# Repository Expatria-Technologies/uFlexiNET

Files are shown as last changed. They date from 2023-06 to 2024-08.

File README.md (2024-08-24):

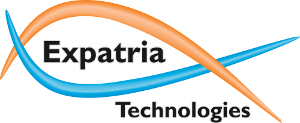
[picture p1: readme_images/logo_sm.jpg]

# uFlexiNET Ethernet and SD card module for FlexiHAL
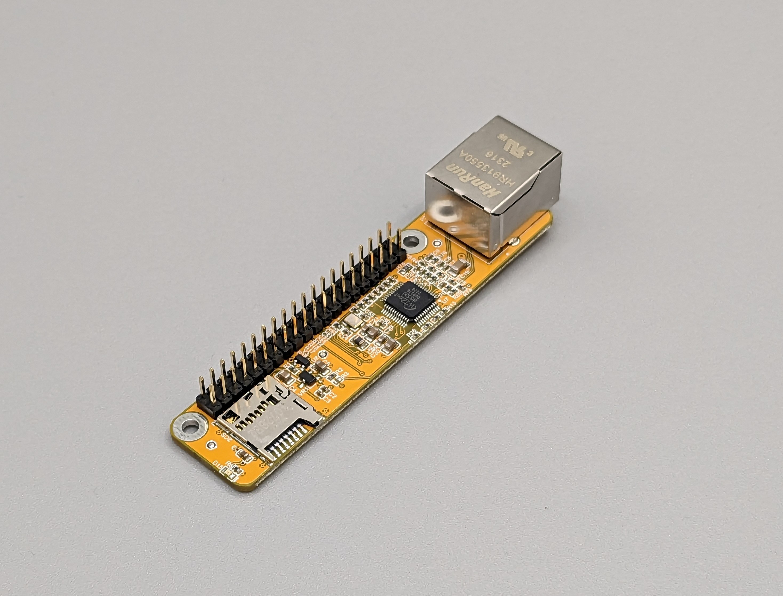
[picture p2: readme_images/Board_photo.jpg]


Adds Ethernet and SD card storage to a FlexiHAL CNC Controller

Currently available in our online store:

[https://expatria.myshopify.com/products/uflexinet](https://expatria.myshopify.com/products/uflexinet-ethernet-and-sd-card-module-for-flexihal)

Please consider buying a board to support our open-source designs. 

This module is designed to be installed on the 40 pin GPIO header of the FlexiHAL CNC controller.  It adds a uSD card interface and an Ethernet interface to the platform.  This brings compatbility with the SD card and Networking plugins with GRBLHAL.  Notably, this allows the use of named files for subroutines, probing routines and automatic toolchanging functions in GRBLHAL.  In addition, the module allows the user to connect compatible senders via Websockets (recomended) or Telnet.  The MQTT plugin can also be used if custom plugin code is written.

To use Remora with this module, users are responsible for researching and compiling their own components.

Optimized GRBLHAL driver is located here.  Look for releases with "ETH" in the name to use this module:  
https://github.com/Expatria-Technologies/STM32F4xx/releases

LinuxCNC/Remora port for uFlexiNET on the FlexiHAL controller is located here:  
https://github.com/Expatria-Technologies/Remora-STM32F4xx-W5500

### Installation
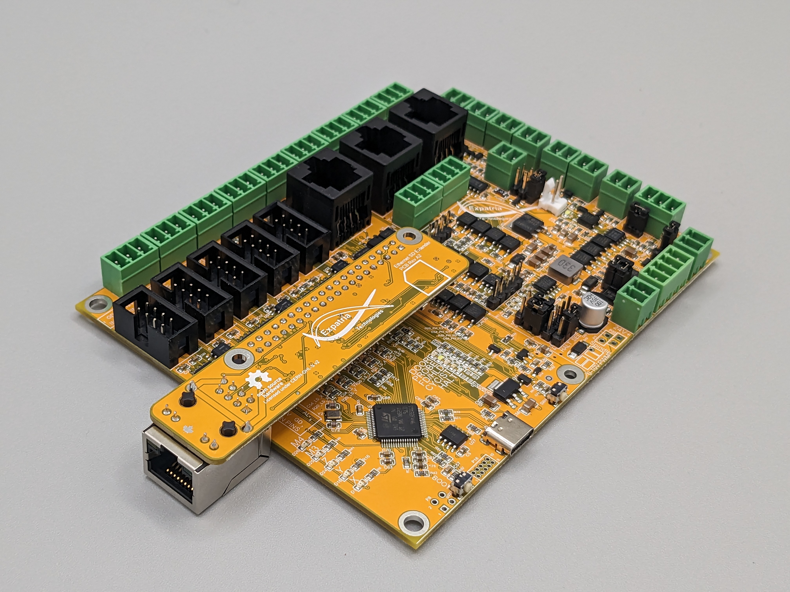
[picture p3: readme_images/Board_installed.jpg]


Disconnect power (main and USB) to the FlexiHAL and install the module in the GPIO header as shown above.  Be aware of excess cable strain (especially with heavy shielded CAT6 Ethernet cables and install spacers, fasteners and strain relief as needed.  If installing an SD card it is recommended to insert it before attaching the uFlexiNET to the mainboard as it is easier to ensure that it has the correct orientation.  Ensure the SD card is formatted as FAT32 and subsequent file operations (upload, delete) can be done via FTP over Ethernet or via the Ymodem protocol in senders like IOSender.

Note that the MCU on Flexi still needs 5V power supplied.  Normally this is via the USBC connector but it is also possible to jumper the 5V bypass pins on flexi to use the onboard 5V regulator.  Please note that this bypasses the galvanic isolation of FLexi and is not generally recommended.  See the FlexiHAL Readme for details:
https://github.com/Expatria-Technologies/Flexi-HAL#power-input

### Usage

Ensure that you flash appropriate GRBLHAL or Remora firmware to your FlexiHAL after installation.  See GRBLHAL and Remora documentation for further usage examples.

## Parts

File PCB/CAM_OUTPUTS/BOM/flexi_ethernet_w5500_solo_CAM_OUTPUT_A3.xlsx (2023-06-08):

Quantity | Manufacturer Part Number 1 | Manufacturer 1 | Description | SuppliersPartNumber | Package | Comment | Designator | Footprint
3 |  |  | Chip capacitors | C19666 | 0603 | 4.7uF | C1, C21, C48 | 0603_C
2 |  |  | Chip capacitor | C52923 | 0402 | 1.0uF | C2, C10 | 0402_C
8 |  |  | Chip capacitors | C1525 | 0402 | 100nF | C3, C22, C23, C24, C25, C26, C29, C50 | 0402_C
4 |  |  | Chip capacitors | C2922481 | 0805 | 22uF | C4, C5, C20, C30 | 0805_C
2 |  |  | Chip capacitors | C15195 | 0402 | 10nF | C6, C53 | 0402_C
2 |  |  | Chip capacitors | C1542 | 0402 | 6.8nF | C7, C8 | 0402_C
1 |  |  | Chip capacitors | C1532 | 0402 | 22nF | C9 | 0402_C
1 |  |  | Chip capacitors | C35216 | 1206 | 1nF | C19 | 1206_C
1 |  |  | Chip capacitor | C23733 | 0402 | 4.7uF | C51 | 0402_C
2 |  |  | Chip capacitors | C32949 | 0402 | 10pF | C54, C55 | 0402_C
1 |  |  | LED | C72043 | 0603 | 0603 Green | D15 | 0603_LED_S1
1 |  |  | 220Ω @ 100MHz 1 2A 150mΩ 0805 Ferrite Beads ROHS | C139188 | 0805 | 220Ω @ 100MHz 1 2A | L6 | 0805_C
1 |  |  | HR911105A Ethernet Interface Arduino Platform Evaluation Expansion Board | C163507 | None | Magjack | P2 | HANRUN_HR911105A
1 |  |  | Header, 20-Pin, Dual row | C124383 |  | Header 20X2 | P3 | HDR2X20_2.54_180
3 |  |  | Chip resistor | C17168 | 0402 | 0Ω ±1% | R1, R2, R18 | 0402_R
4 |  |  | Chip resistor | C25120 | 0402 | 49.9Ω ±1% | R4, R5, R74, R75 | 0402_R
1 |  |  | Chip resistor | C25900 | 0402 | 4.7KΩ ±1% | R6 | 0402_R
2 |  |  | Chip resistor | C25104 | 0402 | 330Ω ±1% | R12, R16 | 0402_R
4 |  |  | Chip resistor | C25744 | 0402 | 10KΩ ±1% | R13, R14, R15, R26 | 0402_R
1 |  |  | Chip resistor | C26083 | 0402 | 1MΩ ±1% | R17 | 0402_R
4 |  |  | Chip resistor | C25105 | 0402 | 33Ω ±1% | R69, R70, R73, R77 | 0402_R
1 |  |  | Chip resistor | C25077 | 0402 | 10Ω ±1% | R76 | 0402_R
1 |  |  | Chip resistor | C22865 | 0603 | 12.4KΩ ±1% | R78 | 0603_R
1 |  |  | Micro SD Connector, Pitch 1.1 mm, 8 Position, Height 1.4 mm, -25 to 85 degC, RoHS, Tape and Reel | C428492 |  | 503398-1892 | SD2 | MOLX-503398-1892_V
1 |  |  | Ethernet Controllers 2.97V ~ 3.63V 10/100 Base-T/TX PHY SPI LQFP-48_7x7x05P Ethernet ICs ROHS | C32843 | LQFP-48_7x7x05P | W5500 | U7 | LQFP-48_7x7x05P
1 |  |  | IC MPU SUPERVISORY 2.93V SOT23 | C9965 | 318-08 | MAX809STRG | U8 | FP-318-08-MFG
1 |  |  | 200mA 680mV@(100mA) Fixed 3.3V~3.3V Positive 1 6V SOT-23-3L Linear Voltage Regulators (LDO) ROHS | C5446 | SOT-23 | XC6206P332MR | VR1 | SOT-23-3L
1 |  |  | Crystal or Oscillator | C13740 |  | 25.0 MHz | Y3 | YSX321SL

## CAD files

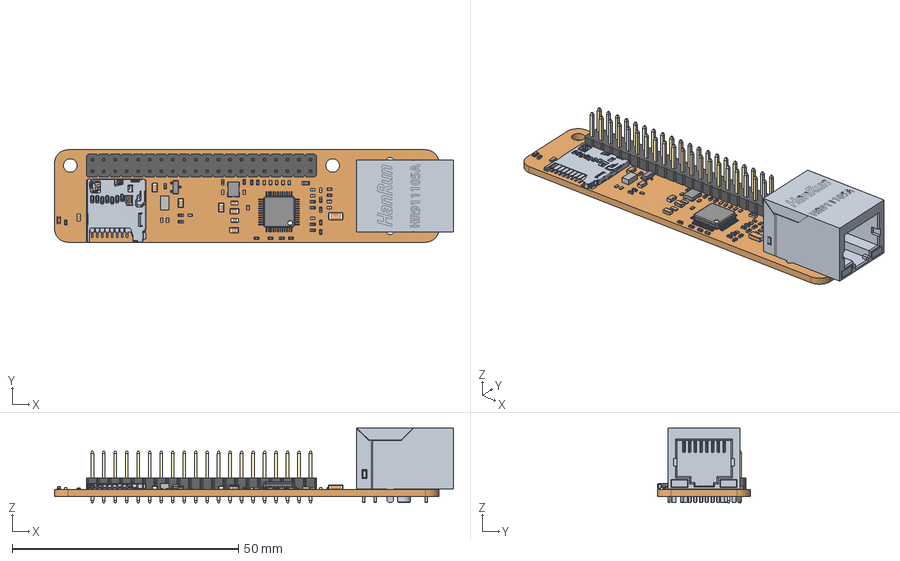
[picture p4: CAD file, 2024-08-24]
uFlexiNet.step
88.2 x 20.5 x 16.5 mm
0402 SMD Capacitor x 18
User Library-RES_1005-0402 x 21
Extruded
User Library-0805 SMD Capacitor x 5
User Library-0603 SMD Capacitor x 3
User Library-RES_1609-0603
User Library-LED_0603_R_Pocket002
User Library-LED_0603_R_Pad004
User Library-LED_0603_R_Fillet
User Library-LED_0603_R_Pocket001
User Library-LED_0603_R_Pad
C1206
pin_header_awl254-dg-g40d
Pins
QFP48P50_900X900X160L60X19N

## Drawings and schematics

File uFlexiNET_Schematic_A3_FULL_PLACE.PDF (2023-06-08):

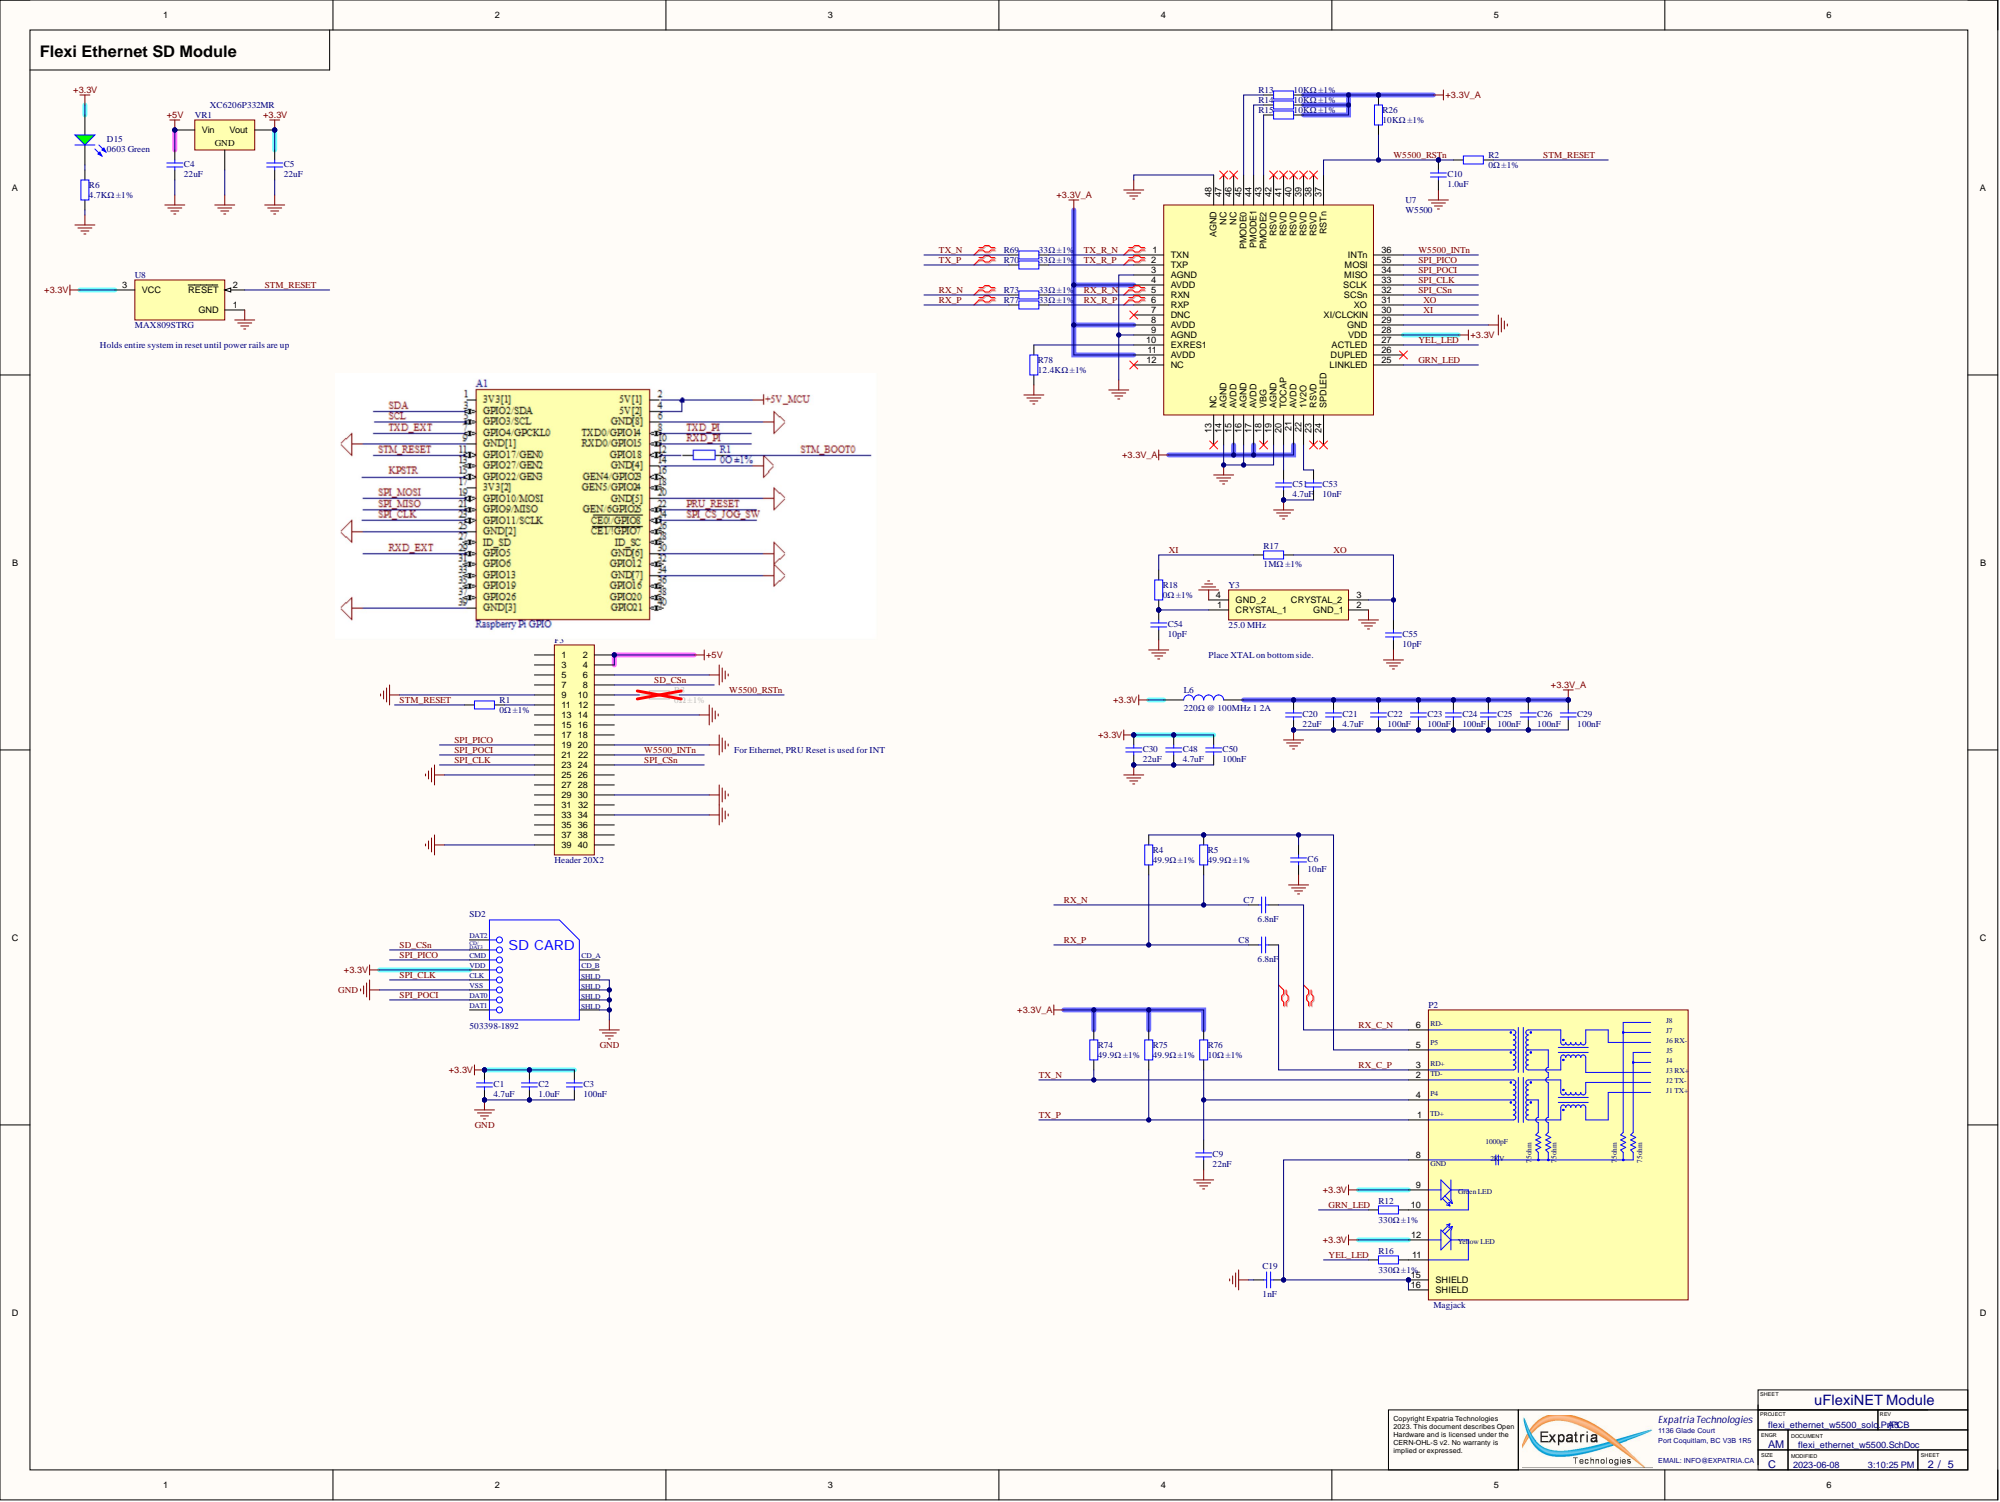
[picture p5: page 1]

Flexi Ethernet SD Module

R14 | 10KΩ ±1%
R15 | 10KΩ ±1%

RSTn 37 RSVD 38 RSVD 39 RSVD 40 RSVD 41 RSVD 42 PMODE2 43 PMODE1 44 PMODE0 45 NC 46 NC 47 AGND 48

SPDLED 24 LINKLED 25 DUPLED 26 ACTLED 27 VDD 28 GND 29 XI/CLCKIN 30 XO 31 SCSn 32 SCLK 33 MISO 34 MOSI 35 INTn 36

TX_R_P | TXP 2

AGND 3
AVDD 4

RX_R_N | | RXN 5
RX_R_P | | RXP 6

DNC 7

AGND 9

Holds entire system in reset until power rails are up

AVDD 11

For Ethernet, PRU Reset is used for INT

9 | GND

2023. This document describes Open Hardware and is licensed under the CERN-OHL-S v2. No warranty is implied or expressed. | | PROJECT | REV A3

flexi_ethernet_w5500_solo.PrjPCB Copyright Expatria Technologies

AM ENGR | DOCUMENT flexi_ethernet_w5500.SchDoc

C | MODIFIED 2023-06-08 3:10:25 PM | SHEET 2 / 5

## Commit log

2023-06-08 Initial commit of project files.
    [flexi_ethernet_w5500.SchDoc, flexi_ethernet_w5500_solo.PrjPCB, flexi_ethernet_w5500_solo_CAM_OUTPUT_A2.csv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]
2023-06-08 Commit A3 files and readme.
    [flexi_ethernet_w5500.SchDoc, flexi_ethernet_w5500_solo_CAM_OUTPUT_A2.xlsx, flexi_ethernet_w5500_solo_CAM_OUTPUT_A3.csv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]
2024-08-24 add step file.
    [uFlexiNet.step]
